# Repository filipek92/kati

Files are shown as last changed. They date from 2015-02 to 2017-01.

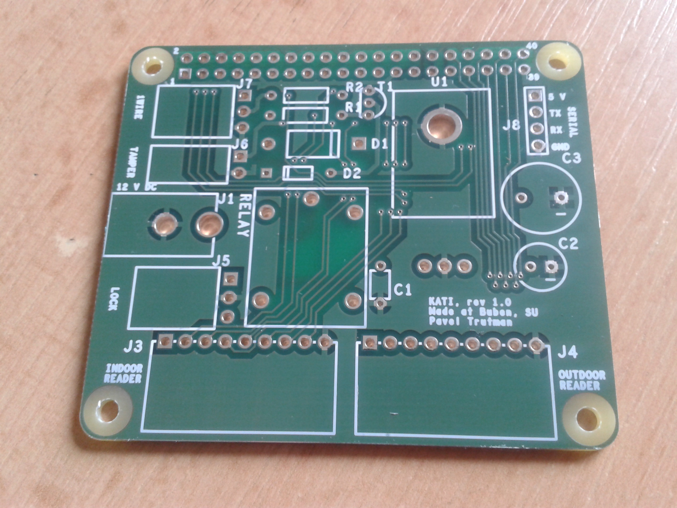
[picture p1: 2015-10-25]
images/IMG_20151021_144417.jpg

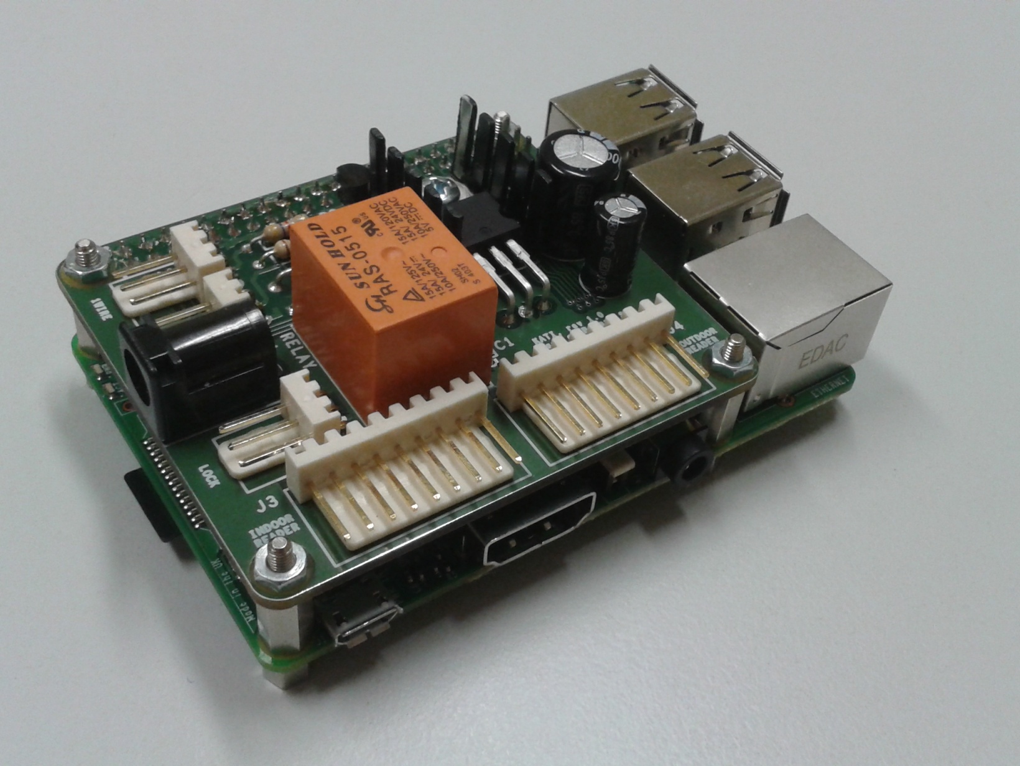
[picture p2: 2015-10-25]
images/IMG_20151023_213506.jpg

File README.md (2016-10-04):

# kati - card access system

Kati is access system developed for [club Buben](http://www.buk.cvut.cz) of [CTU Student Union](http://su.cvut.cz).

Authentication and authorization is performed by these steps:

1. user attaches identification card to reader located near the door
2. reader parses identification of the card
3. authorization request is send to IS to perform authorization and authentication
3. access to the door is granted or denied according to reply from IS server

[RaspberryPi](https://www.raspberrypi.org/) is used as remote controller located near the door.

## Deployment

Assuming you have working SSH key-based login to hosts:

```sh
cd deploy
vim hosts # edit according to your needs
ansible-playbook deploy.yml
```

## Testing

SSH to a testing Raspberry and run:

```sh
cd ~/kati
python3 start.py
```

You can also try only specific components:

```sh
python3 -m kati.reader
python3 -m kati.lock
```

Or run tests (which are heavily WIP):

```sh
python3 -m nose
```

## Developers

- [Pavel Trutman](https://github.com/PavelTrutman)
- [Tomáš Bedřich](https://github.com/tomasbedrich)
- [Tomáš Kukrál](https://github.com/tomkukral)

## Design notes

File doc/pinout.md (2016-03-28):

# Pinout of the header at RPi 2

### I2C
| Pin/GPIO number | Function | IN/OUT |
|:---:|:---:|:---:|
| 3/2 | SDA | IN/OUT |
| 5/3 | SCL | OUT |

### Serial port
| Pin/GPIO number | Function | IN/OUT |
|:---:|:---:|:---:|
| 8/14 | TXD | OUT |
| 10/15 | RXD | IN |

### Card readers
| Indoor reader | Outdoor reader | Function | IN/OUT |
|:---:|:---:|:---:|:---:|
| 18/24 | 32/12 | Beeper (yellow) | OUT |
| 19/10 | 33/13 | Hold (blue) | OUT |
| 21/9 | 35/19 | Data 0 (green) | IN |
| 22/25 | 36/16 | Data 1 (white) | IN |
| 23/11 | 37/26 | Green LED (orange) | OUT |
| 24/8 | 38/20 | Red LED (brown) | OUT |
| 26/7 | 40/21 | Tamper (violet) | IN |

### Lock
| Pin/GPIO number | Function | IN/OUT |
|:---:|:---:|:---:|
| 11/17 | HIGH: locked, LOW: open | OUT |

### Tamper
| Pin/GPIO number | Function | IN/OUT |
|:---:|:---:|:---:|
| 15/22 | HIGH: tampered, LOW: OK | IN |

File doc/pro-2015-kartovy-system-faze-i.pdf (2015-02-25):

PROJEKT KLUBU BUBEN
KARTOVÝ SYSTÉM – FÁZE I.
Odpovědný orgán: | Výbor IT
Řešitelé: | Pavel Trutman, Tomáš Kukrál

Představení projektu:

Současný kartový systém je pro naše účely nedostačující, často padá a je nespolehlivý. Protože k němu neexistuje téměř žádná dokumentace, není na koleji nikdo, kdo by věděl, jak funguje a uměl by jej spravit v případě, že se rozbije. Je tedy na nejvýš nutné vytvořit nový kartový systém.

Aby byl nový systém pokud možno jednoduchý a snadno rozšiřitelný, rozhodli jsme se jej postavit na platformě Raspberry Pi. Každé dveře budou ovládány jedním tímto modulem, který bude do sítě připojen a napájen přes ethernet. Dále bude komunikovat typicky se dvěma čtečkami karet a ovládat elektronický zámek dveří. Celý systém by měl být chráněn proti výpadku proudu (UPS) i výpadku sítě (lokální databáze). Nastavení oprávnění přístupů se bude řídit statusem člověka a časem přístupu a bude se nastavovat ve webovém rozhraní v Kristýnce.

První fáze toho projektu má za cíl sestavit funkční prototyp, na něm systém otestovat a navrhnout případné změny.

Rozpočet a kalkulace:

Čtečky karet a elektronické zámky již máme, nebudeme kupovat další.

2x RaspberryPi 2 + Doprava http://cz.rs-online.com/web/p/processor-microcontroller-development-kits/832-6274 | 2x 1 053,- Kč + 175 Kč
2x micro SD karta (4GB) http://www.czc.cz/verbatim-micro-sdhc-4gb-class-4_2/164705/produkt | 2x 88,- Kč
2x kabel napájecí microUSB http://www.czc.cz/gembird-micro-usb-2-0-am-mbm5p-1m/152207/produkt | 2x 68, - Kč

Propojovací kabely + Doprava http://eshop.minidroid.cz/propojovac-drty/147-premium-female-female-jumper-wires-40-x-6.html | 175,- Kč + 75 Kč
Ostatní drobné součátky (většinou z GME) | do 500, - Kč

Všechny ceny jsou uvedeny včetně DPH.

Celkový rozpočet: 3400 Kč

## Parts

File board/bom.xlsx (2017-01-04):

Supplier | Part-ID | Qty | Value | Device | Package | Parts | Description | MF | MPN | OC_NEWARK | PACKAGE | SUPPLIER | TOLERANCE | VALUE | VOLTAGERATING | aktualni pocet | Kolik je potreba: | pozn:
GME | 832-009 | 1 | BL840GD | PINHD-2X20 | 2X20 | JP1 | PIN HEADER |  |  |  |  |  |  |  |  | 1 | 6 | Mame: 1 shield
GME | 906-096 | 3 | 100n | C-EUC0805 | C0805 | C2, C5, C6 | CAPACITOR, European symbol |  |  |  |  |  |  |  |  | 18 | 3 | Chceme: +5
GME | 901-189 | 2 | 150R | R-EU_R0805 | R0805 | R8, R9 | RESISTOR, European symbol |  |  |  |  |  |  |  |  | 6 | 8 | Celkem 6
GME | 917-016 | 2 | 1N4007 | DIODE-DO-214AC | DO-214AC | D3, D7 | DIODE |  |  |  |  |  |  |  |  | 7 | 7 | + jeden rezerva
GME | 901-178 | 1 | 1k | R-EU_R0805 | R0805 | R11 | RESISTOR, European symbol |  |  |  |  |  |  |  |  | 6 | 1 | Celkem 7 sad
GME | 901-594 | 4 | 1k7 | R-EU_R0805 | R0805 | R1, R2, R4, R5 | RESISTOR, European symbol |  |  |  |  |  |  |  |  | 14 | 14
Farnell | 1759177 | 1 | 2.2uF/100V | C-EUC1206 | C1206 | C3 | CAPACITOR, European symbol |  |  |  |  |  |  |  |  | 6 | 1
GME | 800-168 | 1 | 22-05-7028-02 | 22-05-7028-02 | 7395-02 | J2 | CONNECTOR |  |  | unknown |  |  |  |  |  | 0 | 7
GME | 800-164 | 1 | 22-05-7038-03 | 22-05-7038-03 | 7395-03 | J3 | CONNECTOR |  |  | unknown |  |  |  |  |  | 9 | 0
Farnell | 1539514 | 2 | 220u | EEE-FP1V221AP-CASE-F | CAPAE830X1050N | C1 | Aluminum Electrolytic Capacitors,Surface Mount Type |  | EEE-FP1V221AP | 94M7043 | CASE-F | PANASONIC | ±20 % | 220UF | 35V | 4 | 10
GME | 901-188 | 2 | 4k7 | R-EU_R0805 | R0805 | R6, R7 | RESISTOR, European symbol |  |  |  |  |  |  |  |  | 7 | 7
GME | 901-631 | 2 | 560R | R-EU_R0805 | R0805 | R10, R12 | RESISTOR, European symbol |  |  |  |  |  |  |  |  | 7 | 7
GME | 901-394 | 1 | 5K6 | R-EU_R0805 | R0805 | R3 | RESISTOR, European symbol |  |  |  |  |  |  |  |  | 6 | 1
GME | 901-368 | 1 | 860R | R-EU_R0805 | R0805 | R13 | RESISTOR, European symbol |  |  |  |  |  |  |  |  | 6 | 1
GME | 912-032 | 1 | BC817 | BC817-40 | SOT23-BEC | T1 | NPN Transistror |  |  |  |  |  |  |  |  | 6 | 1
GME | 919-008 | 4 | BZV55C3.0SMD | DIODE-MINIMELF | MINIMELF | D1, D2, D4, D5 | DIODE |  |  |  |  |  |  |  |  | 14 | 14
GME | 634-246 | 1 | G5L | RAS0515 | G5LE | K1 | RELAY |  |  | unknown |  |  |  |  |  | 0 | 7
Farnell | 1469195 | 1 | LM2596S-5.0 | LM2596S-5.0 | TO170P1435X465-6N | U1 | Step-Down Voltage Regulator |  | LM2596S-50 | 41K3844 | TO-263-5 | National |  |  |  | 2 | 5
GME | 969-012 | 1 | LM75 | LM75_ICN | SO8_LM75 | IC1 | Temperatursensor |  |  |  |  |  |  |  |  | 1 | 6
Farnell | 1597004 | 1 | PPTC1812SMD110/16V | 1812L | 1812L | F1 |  |  |  |  |  |  |  |  |  | 6 | 1
GME | 832-361 | 2 | S1G04 2,54mm | PINHD-1X4 | 1X04 | JP2, JP3 | PIN HEADER |  |  |  |  |  |  |  |  | 6 | 8
GME | 832-373 | 2 | S2G10 | MA05-2 | MA05-2 | SV1, SV2 | PIN HEADER |  |  | unknown |  |  |  |  |  | 2 | 12
GME | 960-023 | 2 | SML-LX0805SUGC-TR | LEDCHIPLED_0805 | CHIPLED_0805 | LED2, LED3 | LED |  |  |  |  |  |  |  |  | 7 | 7
GME | 960-216 | 1 | SML-LXT0805IW-TR | LEDCHIPLED_0805 | CHIPLED_0805 | I.01 | LED |  |  |  |  |  |  |  |  | 3 | 4
Farnell | 2212503 | 1 | SRR1260-680M | WE-PD-7447709680_1260/1245/1280/1210 | WE-PD_1260/1245/1280/1210 | L1 | SMD-Shielded Power Inductors WE-PD |  | 7447709680 | 08P2779 | 1210 | Wuerth Elektronik |  |  |  | 2 | 5
Farnell | 2317398 | 1 | MBRS360BT3G | DIODE-DO214AA | DO214AA | D6 | DIODE |  |  |  |  |  |  |  |  | 4 | 3
GME | 806-328 | 0 | WEALTHMETAL DS-214B | JACK-PLUG0 | SPC4077 | J1 | DC POWER JACK |  |  | unknown |  |  |  |  |  | 0 | 0
GME | 840-011 | 4 |  | KONPC-SPK-5 |  |  | Konektor |  |  |  |  |  |  |  |  | 3 | 25
GME | 840-004 | 20 |  | KONPC-SPK-PI |  |  | PIN rezervní |  |  |  |  |  |  |  |  | 0 | 140
GME | 623-373 | 3 |  | DI4M2X10 nikl VIGAN |  |  | Distanční sloupek |  |  |  |  |  |  |  |  | 0 | 21
GME | 623-361 | 6 |  | DA4M2X05 nikl VIGAN |  |  | Distanční sloupek |  |  |  |  |  |  |  |  | 0 | 42

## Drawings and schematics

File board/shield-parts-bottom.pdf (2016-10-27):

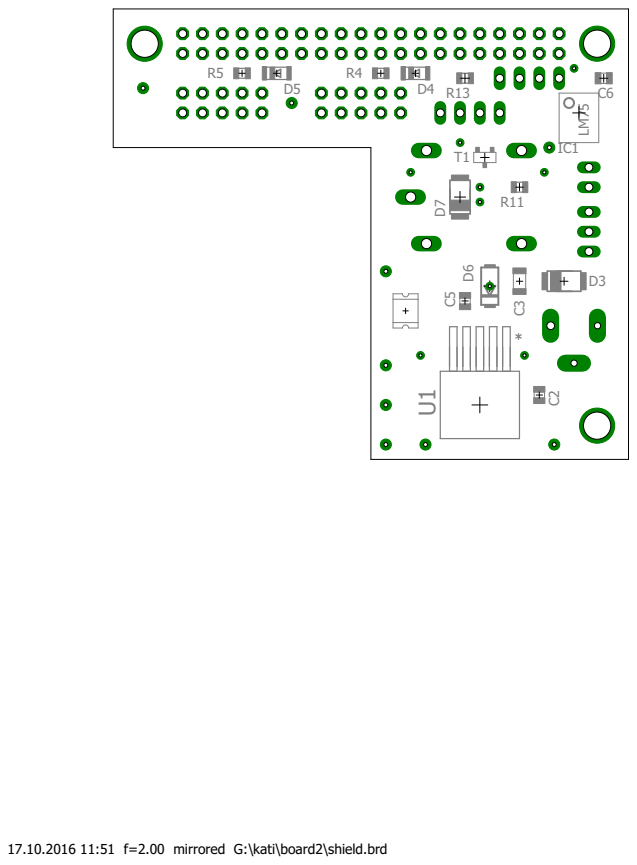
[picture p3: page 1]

17.10.2016 11:51 f=2.00 mirrored G:\kati\board2\shield.brd

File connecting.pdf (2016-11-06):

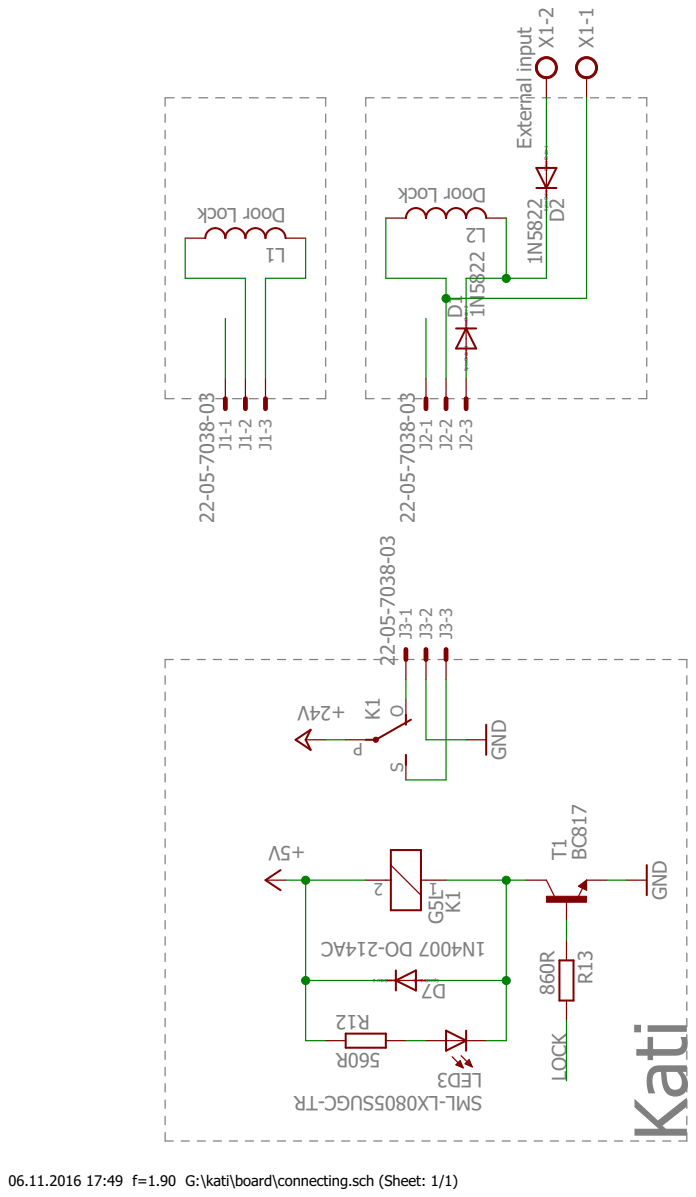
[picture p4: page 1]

06.11.2016 17:49 f=1.90 G:\kati\board\connecting.sch (Sheet: 1/1)

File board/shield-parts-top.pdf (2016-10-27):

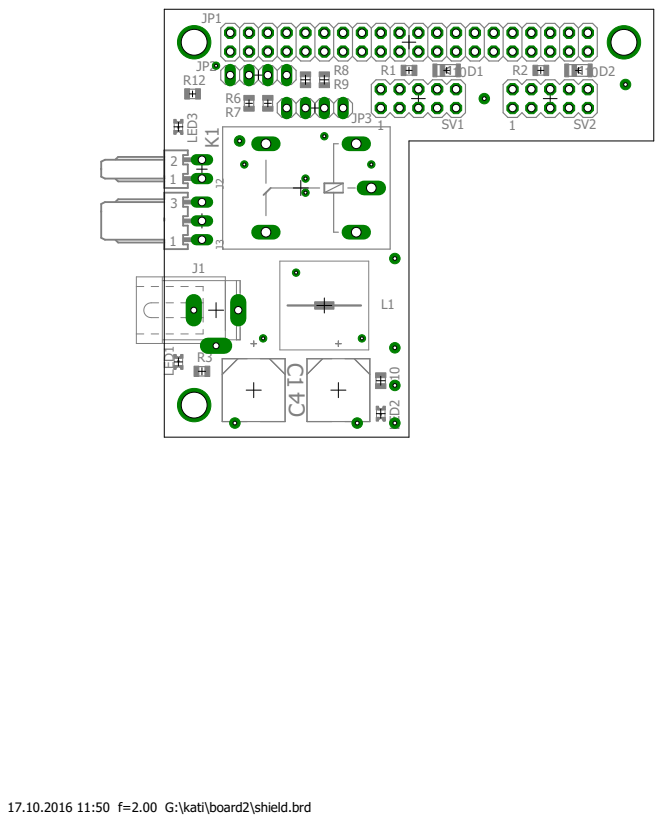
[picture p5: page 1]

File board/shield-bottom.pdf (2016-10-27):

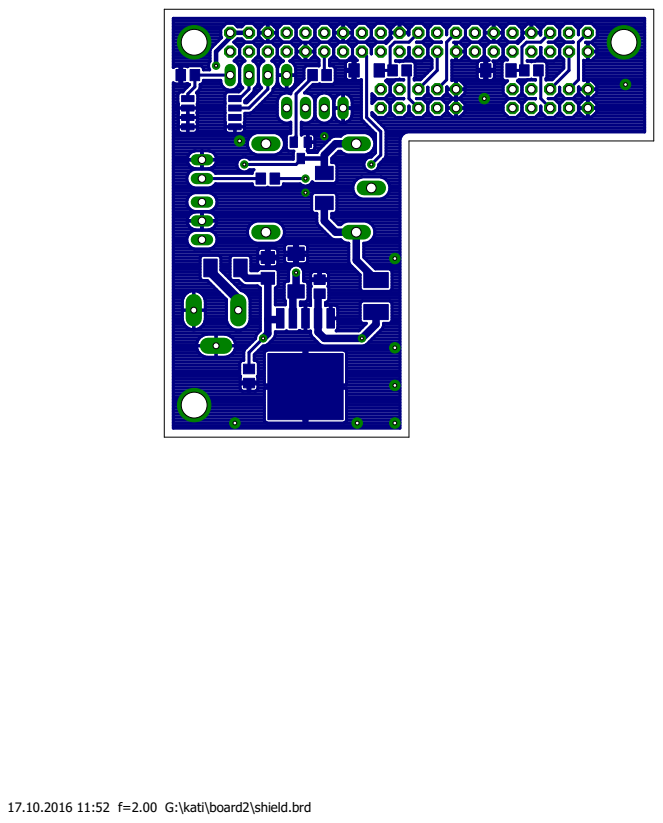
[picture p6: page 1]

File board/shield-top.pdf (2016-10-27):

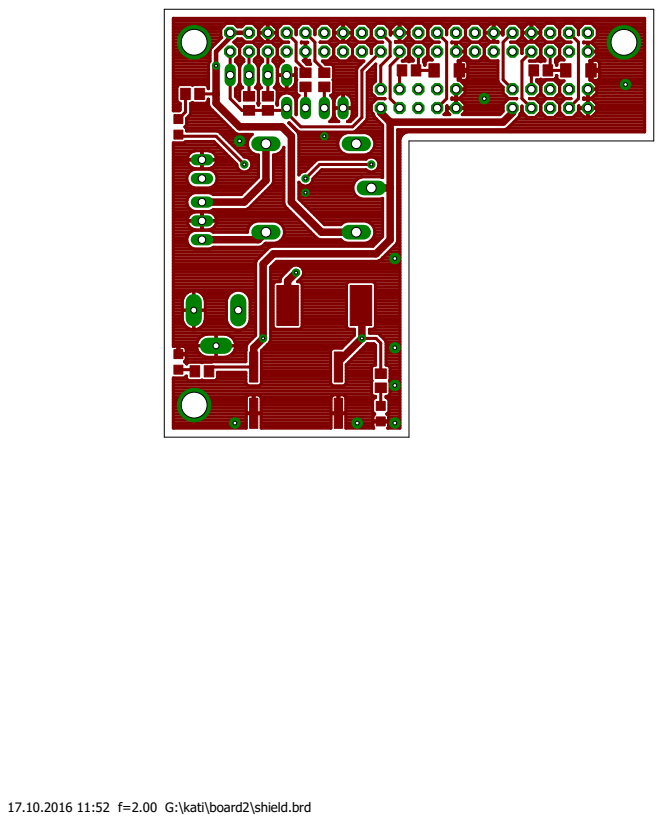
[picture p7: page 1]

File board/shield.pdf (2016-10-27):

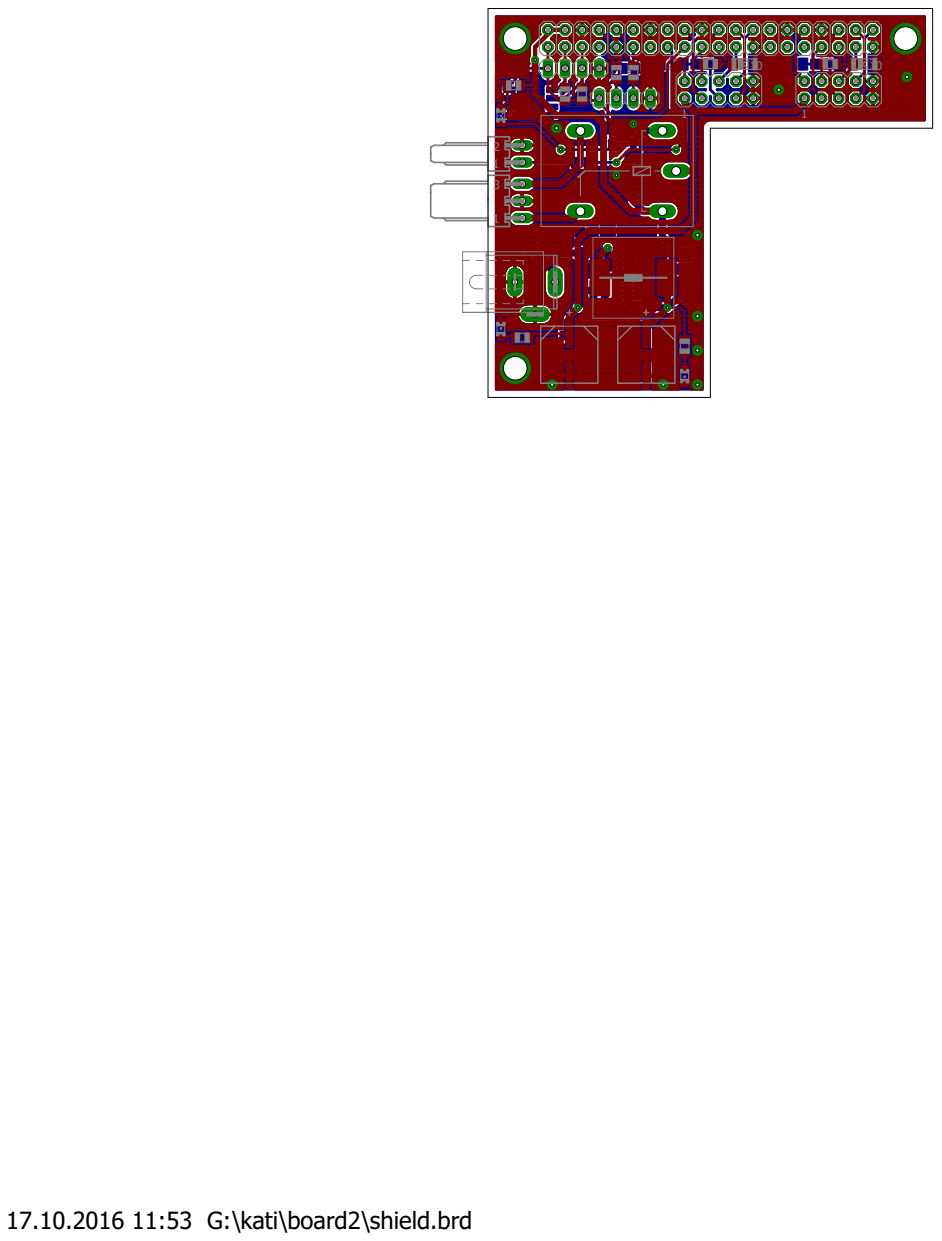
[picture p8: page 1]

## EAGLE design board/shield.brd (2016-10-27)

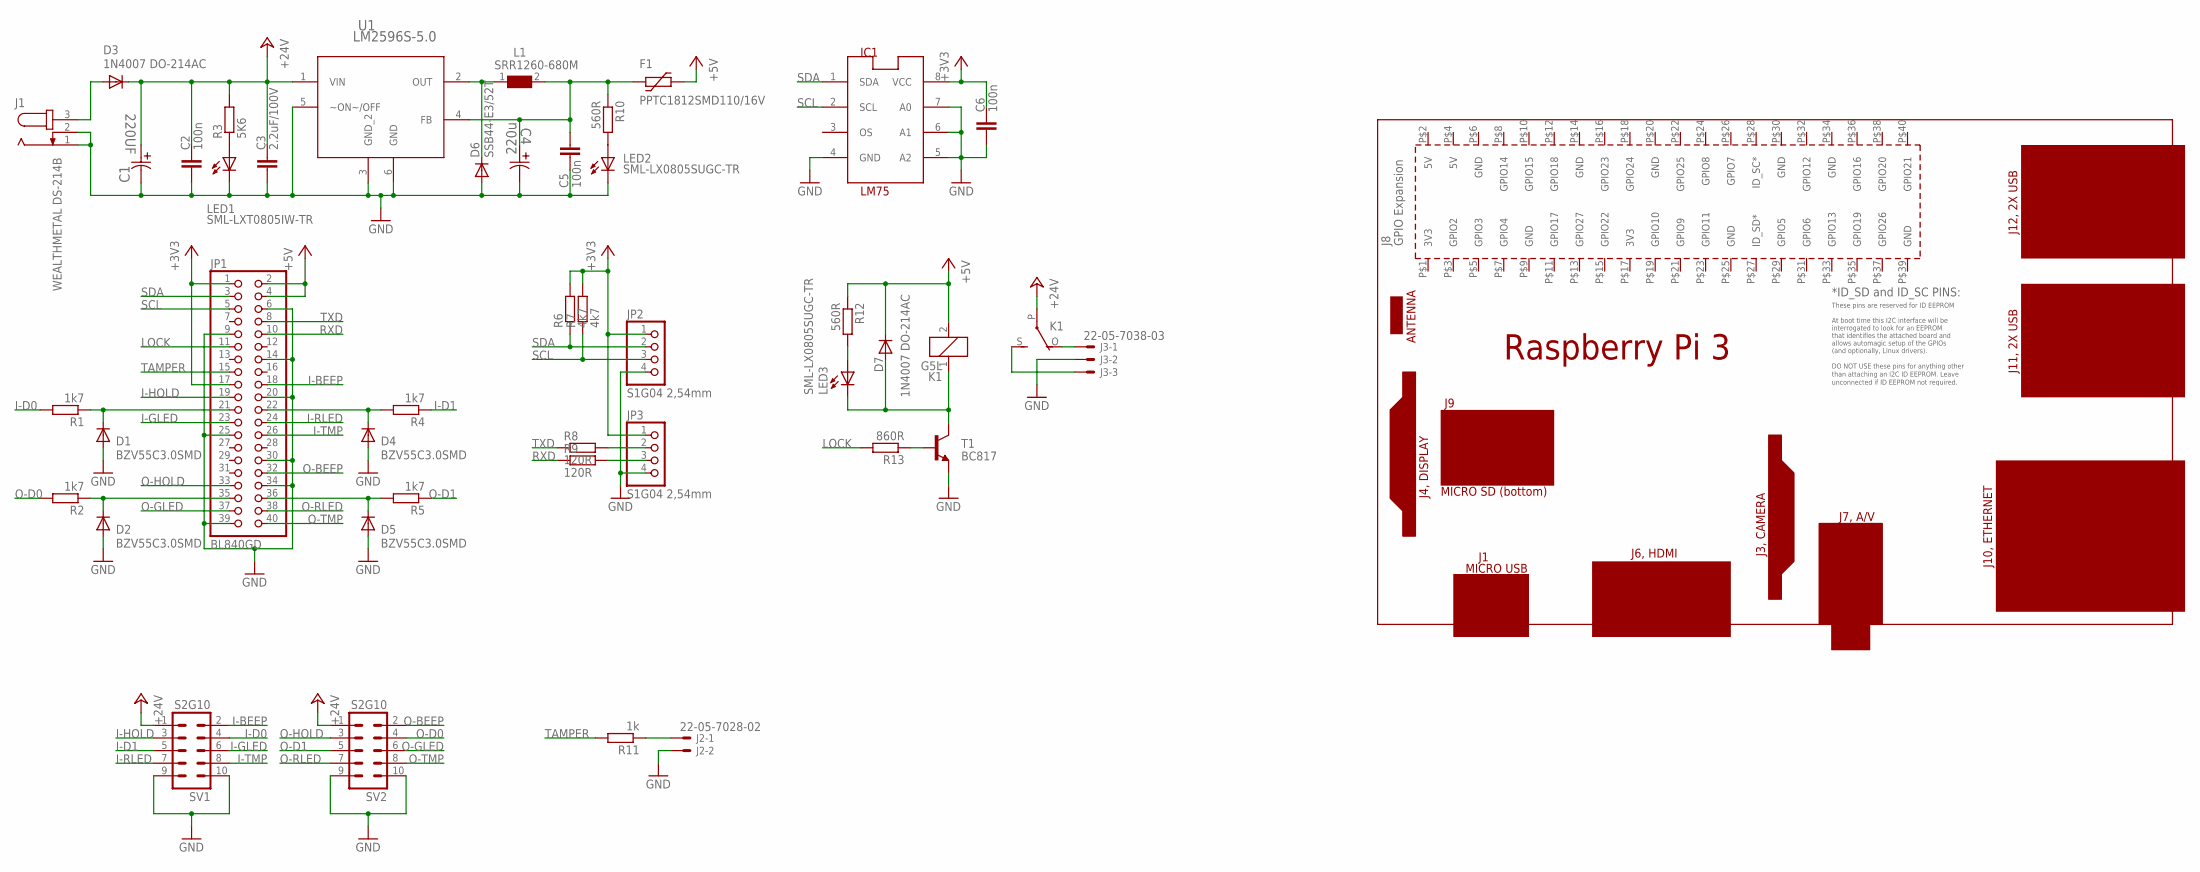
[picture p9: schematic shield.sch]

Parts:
C1: 220UF; CAPAE830X1050N
C2, C5, C6: 100n; C0805
C3: 2.2uF/100V; C1206
C4: 220u; CAPAE830X1050N
D1, D2, D4, D5: BZV55C3.0SMD; MINIMELF
D3, D7: 1N4007 DO-214AC; DO-214AC
D6: SSB44-E3/52T; DO214AA
F1: PPTC1812SMD110/16V; 1812L
IC1: LM75; SO8_LM75
J1: WEALTHMETAL DS-214B; SPC4077
J2: 22-05-7028-02; 7395-02
J3: 22-05-7038-03; 7395-03
JP1: BL840GD; 2X20
JP2, JP3: S1G04 2,54mm; 1X04
K1: G5L; G5LE
L1: SRR1260-680M; WE-PD_1260/1245/1280/1210
LED1: SML-LXT0805IW-TR; CHIPLED_0805
LED2, LED3: SML-LX0805SUGC-TR; CHIPLED_0805
PCB1: RPI3
R1, R2, R4, R5: 1k7; R0805
R3: 5K6; R0805
R6, R7: 4k7; R0805
R8, R9: 120R; R0805
R10, R12: 560R; R0805
R11: 1k; R0805
R13: 860R; R0805
SV1, SV2: S2G10; MA05-2
T1: BC817; SOT23-BEC
U1: LM2596S-5.0; TO170P1435X465-6N

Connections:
+3V3: C6.2, IC1.8 (VCC), JP1.1, JP1.17, JP2.1, JP3.1, R6.2, R7.2
+5V: D7.C, F1.P$2 (2), JP1.2, JP1.4, K1.2, R12.1
+24V: C1.1, C2.2, C3.1, D3.C, K1.P, R3.2, SV1.1, SV2.1, U1.1 (VIN)
GND: C1.2, C2.1, C3.2, C4.2, C5.1, C6.1, D1.A, D2.A, D4.A, D5.A, D6.A, IC1.4 (GND), IC1.5 (A2), IC1.6 (A1), IC1.7 (A0), J1.1, J1.2, J2.2, J3.2, JP1.6, JP1.9, JP1.14, JP1.20, JP1.25, JP1.30, JP1.34, JP1.39, JP2.4, JP3.4, LED1.C, LED2.C, SV1.9, SV1.10, SV2.9, SV2.10, T1.E, U1.3 (GND_2), U1.5 (~ON~/OFF), U1.6 (GND)
I-BEEP: JP1.18, SV1.2
I-D0: R1.2, SV1.4
I-D0-3V3: D1.C, JP1.21, R1.1
I-D1: R4.1, SV1.5
I-D1-3V3: D4.C, JP1.22, R4.2
I-GLED: JP1.23, SV1.6
I-HOLD: JP1.19, SV1.3
I-RLED: JP1.24, SV1.7
I-TMP: JP1.26, SV1.8
LOCK: JP1.11, R13.2
unnamed: C4.1, C5.2, F1.P$1 (1), L1.2, R10.1, U1.4 (FB)
unnamed: J2.1, R11.1
unnamed: JP3.2, R8.2
unnamed: LED2.A, R10.2
unnamed: J3.3, K1.S
unnamed: JP3.3, R9.2
unnamed: J3.1, K1.O
unnamed: D7.A, K1.1, LED3.C, T1.C
unnamed: R13.1, T1.B
unnamed: LED3.A, R12.2
unnamed: LED1.A, R3.1
unnamed: D6.C, L1.1, U1.2 (OUT)
O-BEEP: JP1.32, SV2.2
O-D0: R2.2, SV2.4
O-D0-3V3: D2.C, JP1.35, R2.1
O-D1: R5.1, SV2.5
O-D1-3V3: D5.C, JP1.36, R5.2
O-GLED: JP1.37, SV2.6
O-HOLD: JP1.33, SV2.3
O-RLED: JP1.38, SV2.7
O-TMP: JP1.40, SV2.8
RXD: JP1.10, R9.1
SCL: IC1.2 (SCL), JP1.5, JP2.3, R7.1
SDA: IC1.1 (SDA), JP1.3, JP2.2, R6.1
TAMPER: JP1.15, R11.2
TXD: JP1.8, R8.1
UIN: D3.A, J1.3

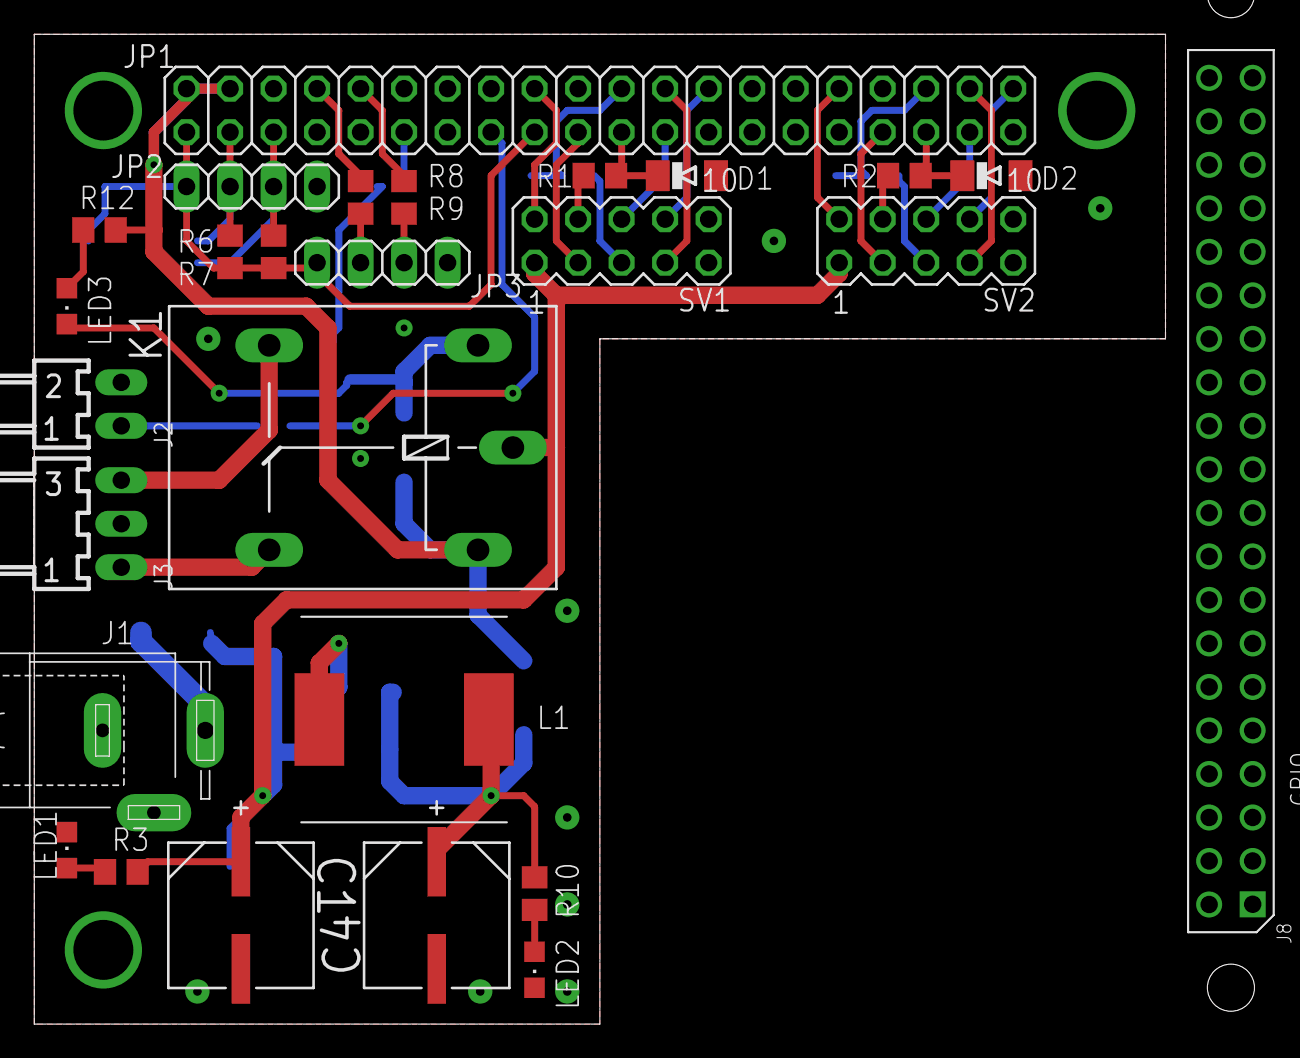
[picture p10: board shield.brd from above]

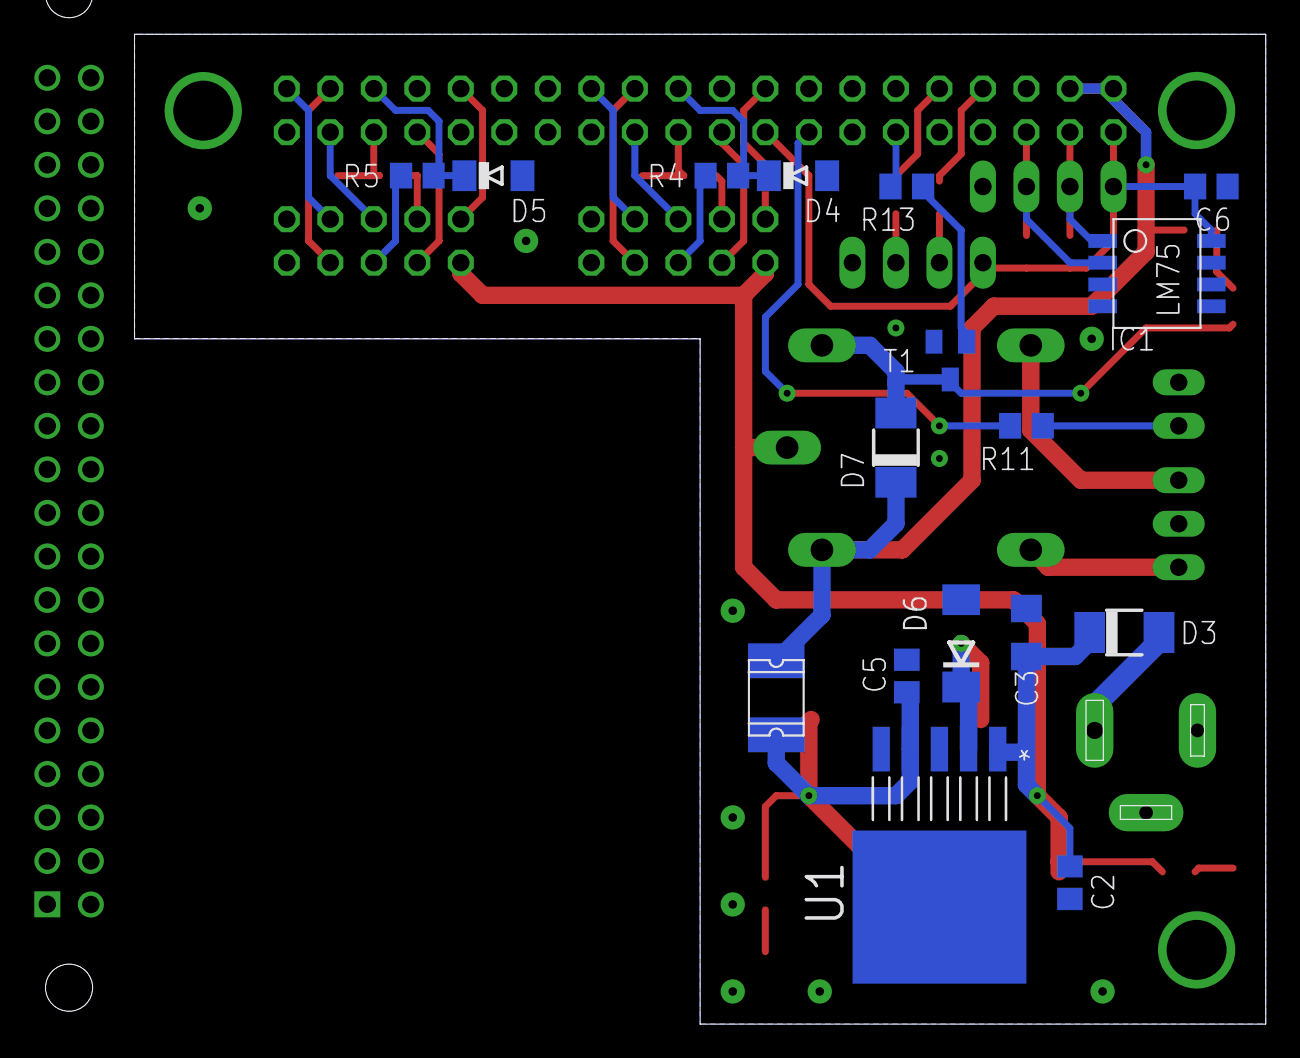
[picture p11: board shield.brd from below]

Board: 2 copper layers, 66.0 x 57.8 mm, 44 parts (17 on the bottom side), 41 nets.

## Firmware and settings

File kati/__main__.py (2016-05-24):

#!/usr/bin/env python3

import pigpio
import time
import logging
import kati.reader
import kati.lock
import kati.kristin


# start logger
logging.basicConfig(level=logging.INFO)
log = logging.getLogger(__name__)


class Kati(object):

    def __init__(self, pi):
        self.pi = pi

        # init physical components
        self.lock = kati.lock.Lock(pi, 17)
        self.reader_indoor = kati.reader.Reader(pi, 24, 10, 9, 25, 11, 8, 7, self._callback_indoor)
        self.reader_outdoor = kati.reader.Reader(pi, 12, 13, 19, 16, 26, 20, 21, self._callback_outdoor)

    def _callback(self, the_reader, card_number):
        # TODO handle timeout
        # TODO use the_reader.text_id as reader ID
        if kati.kristin.has_access(1, card_number):
            # if user has access, unlock
            log.info("access granted")
            self.lock.unlock()
            # TODO cannot send multiple waveforms, need to merge
            # the_reader.green_blink()
        else:
            # otherwise beep
            log.info("access denied")
            the_reader.beep()

    def _callback_indoor(self, num_bits, card_number):
        self._callback(self.reader_indoor, card_number)

    def _callback_outdoor(self, num_bits, card_number):
        self._callback(self.reader_outdoor, card_number)

    def cancel(self):
        self.reader_indoor.cancel()
        self.reader_outdoor.cancel()
        self.lock.cancel()


# init
pi = pigpio.pi()
k = Kati(pi)
log.debug("started")

# main loop
try:
    while True:
        time.sleep(300)
except KeyboardInterrupt:
    pass

# cleanup
log.debug("shutdown")
k.cancel()
pi.stop()

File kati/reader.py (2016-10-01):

#!/usr/bin/env python3

import pigpio
import logging
import kati.wiegand


BEEP_LEN = 2000 * 1000  # in microseconds
GREEN_BLINK_LEN = BEEP_LEN  # in microseconds


def _get_raspberry_serial_number():
    with open("/proc/cpuinfo") as cpuinfo:
        for line in cpuinfo:
            if "Serial" in line:
                return line.split(":")[-1].strip()


class Reader:
    """
    A class representing a physical card reader with all of its capabilities.
    """

    def __init__(self, pi, beeper, hold, data_0, data_1, led_green, led_red,
                 tamper, data_callback, tamper_callback=None, text_id=None):
        """
        Start Wiegand decoder, setup output ports, prepare waves and register callbacks.
        """
        self.pi = pi
        self.hold = hold
        self.led_red = led_red
        self.data_callback = data_callback

        if text_id:
            self.text_id = text_id
        else:
            # no explicit text_id provided - combine this Raspberry's serial
            # number with data_1 gpio (determines indoor/outdoor reader)
            self.text_id = "{}-{}".format(_get_raspberry_serial_number(), data_1)

        # start logger
        self.log = logging.getLogger("{}(text_id={})".format(__name__, self.text_id))

        # start wiegand decoder with passed callback
        self.wiegand = kati.wiegand.decoder(pi, data_0, data_1, self._callback)

        # set output mode and clear values (HIGH = logical 0)
        for port in beeper, hold, led_green, led_red:
            pi.set_mode(port, pigpio.OUTPUT)
            pi.write(port, pigpio.HIGH)

        # prepare waves
        self._setup_beep_wave(beeper)
        self._setup_green_bink_wave(led_green)

        # handle tamper
        if tamper_callback:
            pi.set_mode(tamper, pigpio.INPUT)
            pi.set_pull_up_down(tamper, pigpio.PUD_UP)
            self.cb_tamper = pi.callback(tamper, pigpio.RISING_EDGE, tamper_callback)
        else:
            self.cb_tamper = None

    def _setup_beep_wave(self, beeper):
        # see http://abyz.co.uk/rpi/pigpio/python.html#wave_create
        wf = []
        wf.append(pigpio.pulse(0, 1 << beeper, BEEP_LEN))
        wf.append(pigpio.pulse(1 << beeper, 0, 0))

        self.pi.wave_add_new()
        self.pi.wave_add_generic(wf)
        self.beep_wave = self.pi.wave_create()  # create and save id
        assert self.beep_wave >= 0, "Unable to create beep wave"

    def _setup_green_bink_wave(self, led_green):
        wf = []
        wf.append(pigpio.pulse(0, 1 << led_green, GREEN_BLINK_LEN))
        wf.append(pigpio.pulse(1 << led_green, 0, 0))

        self.pi.wave_add_new()
        self.pi.wave_add_generic(wf)
        self.green_blink_wave = self.pi.wave_create()
        assert self.green_blink_wave >= 0, "Unable to create green blink wave"

    def _callback(self, num_bits, card_number):
        self.log.info("read %d bits, data %s", num_bits, card_number)
        self.data_callback(num_bits, card_number)

    def beep(self):
        """
        Start one time non-blocking beep.
        """
        self.pi.wave_send_once(self.beep_wave)
        self.log.info("beep for %.1f seconds", BEEP_LEN / 1e6)

    def green_blink(self):
        """
        Start one time non-blocking green LED blink.
        """
        self.pi.wave_send_once(self.green_blink_wave)
        self.log.info("green blink for %.1f seconds", GREEN_BLINK_LEN / 1e6)

    def cancel(self):
        """
        Release resources.
        """
        self.pi.wave_delete(self.beep_wave)
        self.pi.wave_delete(self.green_blink_wave)
        if self.cb_tamper:
            self.cb_tamper.cancel()


if __name__ == "__main__":
    # demo
    import time

    def callback(bits, value):
        print("bits={} value={}".format(bits, value))

    pi = pigpio.pi()
    r = Reader(pi, 24, 10, 9, 25, 11, 8, 7, callback)
    time.sleep(300)
    r.cancel()
    pi.stop()

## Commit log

2015-10-07 Kati board
    [KATI.DSN, Kati.brd, art_param.txt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]
2015-10-08 Pour copper in TOP etch layer.
    [Kati.brd]
2015-10-08 Pour copper into BOTTOM etch layer.
    [Kati.brd]
2015-10-08 Fixed some bad diameters of holes.
    [KATI.DSN, Kati.brd, kati_to92.psm]
2015-10-08 Artworks created
    [Kati.brd, art_param.txt, nc_param.txt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]
2015-10-09 Fixed minimal width of lines and spaces.
    [Kati.brd, nc_param.txt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]
2015-10-09 Artwork Outline added.
    [Kati.brd]
2015-10-25 Value of resistor R1 set
    [KATI.DSN]
2015-10-25 Technical data sent to Progoboard to mafacture the PCB.
2015-10-28 Exported wiring diagram and artworks into pdf. Added bill of material.
    [Kati-1-2-np.drl, Kati-1-2.drl]
2016-03-28 Changed (fixed) pins to GPIO numbers
    [reader.py, wiegand.py]
2016-10-04 Added error handling when access request fails
    [kristin.py]
2016-10-17 Shield version 2 created and routed
    [shield.brd, shield.sch]
2016-10-17 Minor changes in PCB design
    [shield.brd]
2016-10-17 Led added, parts renumbered
    [shield.brd, shield.sch]
2016-10-17 Names reordered
    [shield.brd]
2016-10-17 Minor silkscreen changes
    [shield.brd]
2016-10-17 Factory data generated
    [bot.gbr, mill.gbr, plb.gbr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]
2016-10-27 Bill of material
    [bom.xlsx]
2016-10-27 Old board replaced
    [KATI.DSN, Kati.brd, art_param.txt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]
2016-11-06 Added connecting diagram
    [connecting.sch]
2017-01-04 Add aktualni stavy soucastek a kolik je potreba dokoupit do bom.xlsx
    [bom.xlsx]
